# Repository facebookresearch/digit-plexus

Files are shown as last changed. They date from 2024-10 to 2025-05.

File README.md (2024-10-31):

# Meta Digit Plexus
##### A robotics hardware platform for the integration sensors and end effectors into a common platform.

<p align="center">
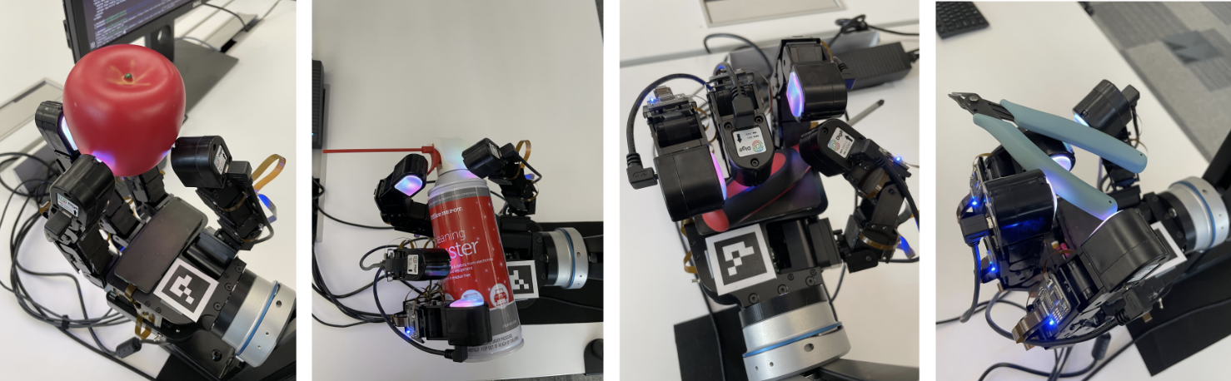
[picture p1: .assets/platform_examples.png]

</p>

<p align="center">
    
</p>

Digit Plexus aims to create a standardized platform that provides a hardware-software solution to integrate tactile sensors on any robot hand. The platform interfaces vision-based and skin-based tactile sensors like Digit, Digit 360, and [ReSkin](https://reskin.dev) across fingertips, fingers, and palm, into control boards to encode all data to a host computer. The software integration and hardware components of the platform allows for seamless data collection, control and analysis over a single cable.

## Standardized Platform

We propose and implement variations of the Digit Plexus standardized architecture found [here](./docs/digit-plexus.pdf)

The [advanced](./hardware/schematics/advanced/) variation of the architecture allows for a modular implementation to support any custom sense patch configuration where each link is connected via USB to the hand logic motherboard. 

Additionally, actions may be provided to a robotic end effector or hand via multiple methods such as: CAN, USB, I2C. 

#### Partnerships

We have partnered with Wonik Robotic's to develop a next generation Allegro Hand based off of the Digit Plexus platform. For early access, interest may be expressed through this [form](https://digit.ml/plexus).

## Usage

Design files for **basic** (rigid based) and **advanced** (flex) are found in the [hardware](./hardware/) folder of the repository. Furthermore, we provide the Altium Designer ECAD templates which can be used to create a custom sensor patch configuration for the hand, links or fingertips. 

### Sense and Hand Patch

Mechanical sense patch files for 3D printing or mold design are found in the [mechanical](./mechanical/) folder. Depending on the application, or the preferred sensing modality, you may use a similar technique to ReSkin (magnetic particulate infused silicone) or an alternative composition of silicone for forming the sensing surface interacting with the sense patch. We recommend attaching the sense patches to the base end effector with a 3M 300LSE double sided adhesive. 

### Fingertip Sensing

The Digit Plexus platform supports Digit tactile sensors as well as any alternative sensor based on a USB2.0 connection as shown [here](./docs/digit-plexus-digit-v1.pdf).

<p align="center">
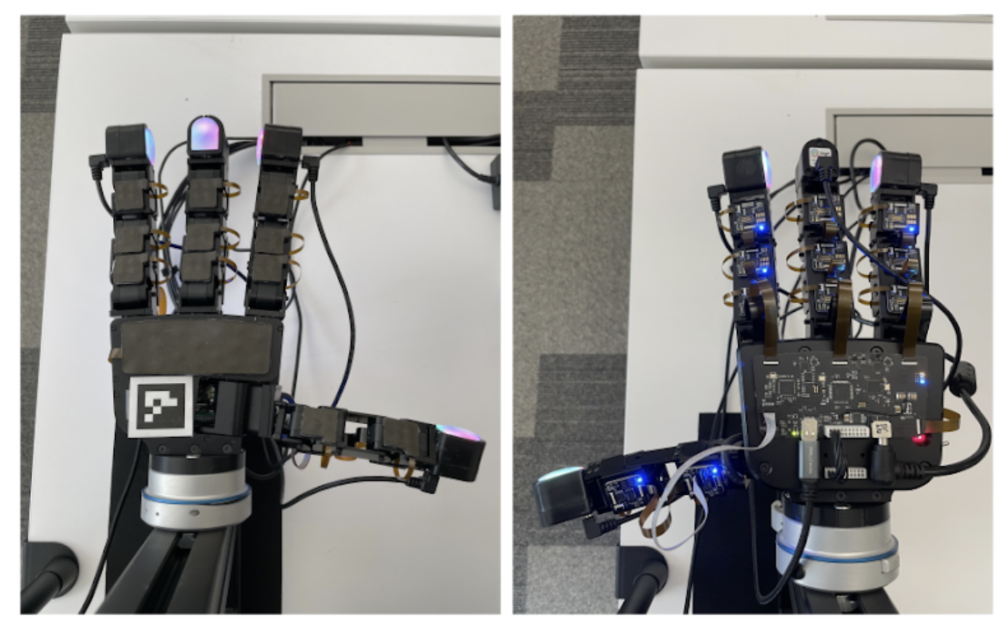
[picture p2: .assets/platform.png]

</p>

## 🛠️Installation and setup
Digit Plexus contains a USB hub device which will enumerate all devices connected to the [base](./hardware/base).

Currently, this supports the [Allegro Hand](https://www.allegrohand.com/) and the [next generation Allegro Hand](https://digit.ml/plexus.html) in partnership with Meta.

Digit Plexus provides a new interface for controlling the Allegro Hand directly through a Python interface, as well provides a ROS2 integration.

Installation and usage instructions are found [here](./plexus/README.md).

## Related Works using Digit Plexus plartform
* [Neural feels with neural fields: Visuo-tactile perception for in-hand manipulation, Sudharshan Suresh et al.](https://suddhu.github.io/neural-feels/)
* [Learning In-Hand Translation Using Tactile Skin With Shear and Normal Force Sensing, Jessica Yin et al.](https://jessicayin.github.io/tactile-skin-rl/)

## License
This project is licensed under [LICENSE](LICENSE).

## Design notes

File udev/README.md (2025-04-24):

# Device Install
Scripts necessary to install physical devices, configure permissions and attributes. 

### Install `udev` Device Rules

```
sudo ./install_devices.sh
```

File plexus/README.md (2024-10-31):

# Digit Plexus 
This guide will help you set up the environment, build the ROS2 package Digit Plexus , and join the growing community of developers and researchers.

## 🛠 Virtual Environment Setup

To install and activate the virtual environment for Digit Plexus, run the following commands:

```
cd digit-plexus
./plexus/install_plexus_venv.sh
```
This will handle the necessary dependencies and ensure your environment is ready for development.

## 🛠 Build ROS2 pkg
```
mkdir -p plexus_ws/src
cd plexus_ws/src
git clone https://github.com/facebookresearch/digit-plexus.git
cd ..
sh ./src/digit-plexus/plexus/ros2/plexus_pkg/colcon_build.sh
```

## 🛠 Install Digit Plexus  pkg
```
cd plexus_ws/src/digit-plexus/
pip install -e .
```

This creates the workspace, builds the source, and prepares everything for use with ROS2 nodes and topics.

## 🚀 Run Commands 
To launch the Digit Plexus package, use the following command:

This launches the allegro hand with plexus.
```bash
ros2 launch plexus_pkg allegro_hand_launch.py
```

For Sensor Patch
```
ros2 launch plexus_pkg sensor_patch_launch.py
```

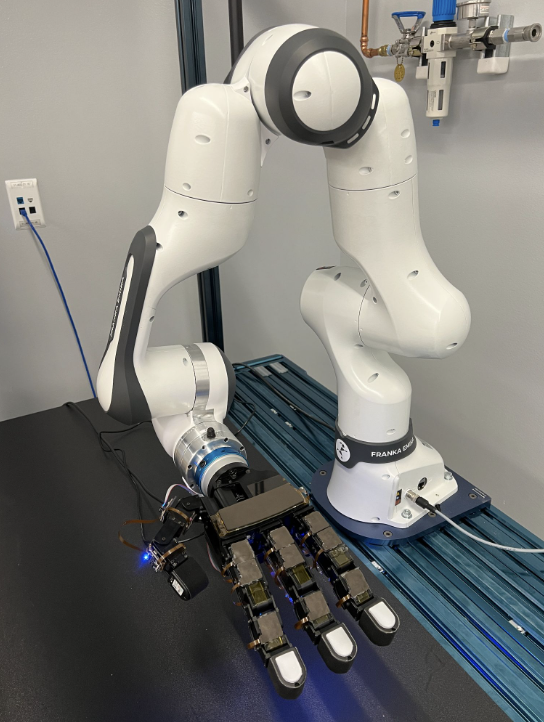
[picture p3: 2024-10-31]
.assets/arm_platform.png

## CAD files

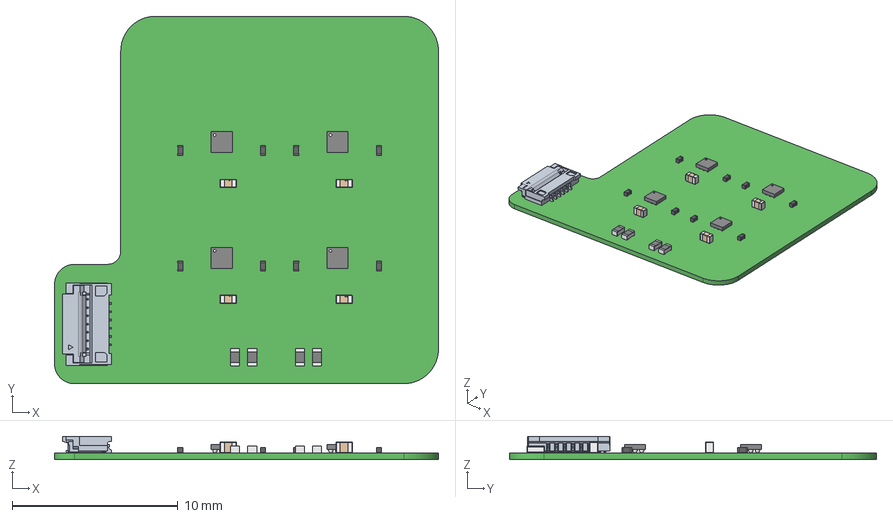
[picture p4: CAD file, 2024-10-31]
mechanical/plexus_finger_link_sense_patch.step
23.2 x 22.2 x 1.41 mm
ball x 36
Mid_Body x 4
Mark x 4
TDK Logo x 4
Cap_Murata_GRM155R71C104KA88D_eec x 8

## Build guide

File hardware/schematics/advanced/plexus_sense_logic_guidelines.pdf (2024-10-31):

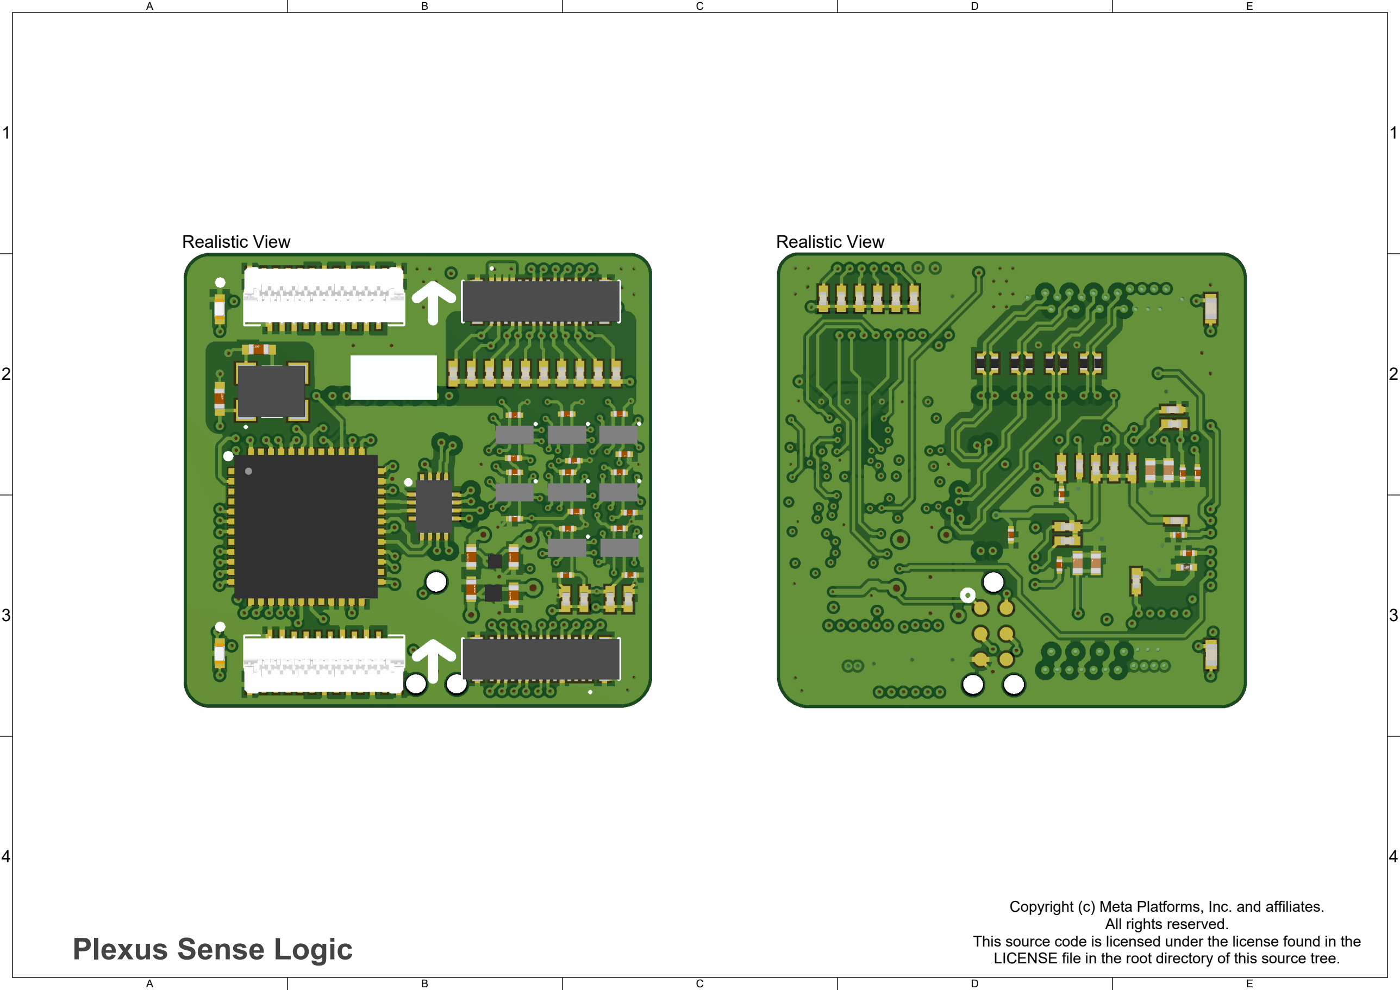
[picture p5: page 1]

A

B

C

D

E

1 | 1
2 | 2
3 | 3
4 | 4
Realistic View | Realistic View

# Plexus Sense Logic

Copyright (c) Meta Platforms, Inc. and affiliates.
All rights reserved.
This source code is licensed under the license found in the LICENSE file in the root directory of this source tree.

1 | 1
2 | 2
3 | 3
4 | 4

STACKUP SUMMARY:
A. NUMBER OF COPPER LAYERS: 8
B. BOARD THICKNESS SHALL BE 1.6mm +/- 10%
C. COPPER: See Layer Stack
D. DEFAULT TRACE/SPACE: 5mil / 5mil
E. CONDUCTOR WIDTH TOLERANCE = +/- 0.01mm

1.

2. SURFACE FINISH/PLATING: ENIG
SOLDERMASK WITH LIQUID PHOTO IMAGEABLE (LPI) PER IPC-SM-840C, CLASS T. COLOR: MATTE BLACK

3.

LOCATE MANUFACTURER'S IDENTIFICATION AND LOT CODE ON PRIMARY SIDE FREE FROM ALL METAL ENTITY RENDERED IN SILKSCREEN.

4.

DETAILS NOT SPECIFIED ARE AT MANUFACTURER'S OPTION BUT FINAL APPROVAL MUST BE OBTAINED

5.

NOTES: UNITS IN MILLIMETERS UNLESS OTHERWISE SPECIFIED

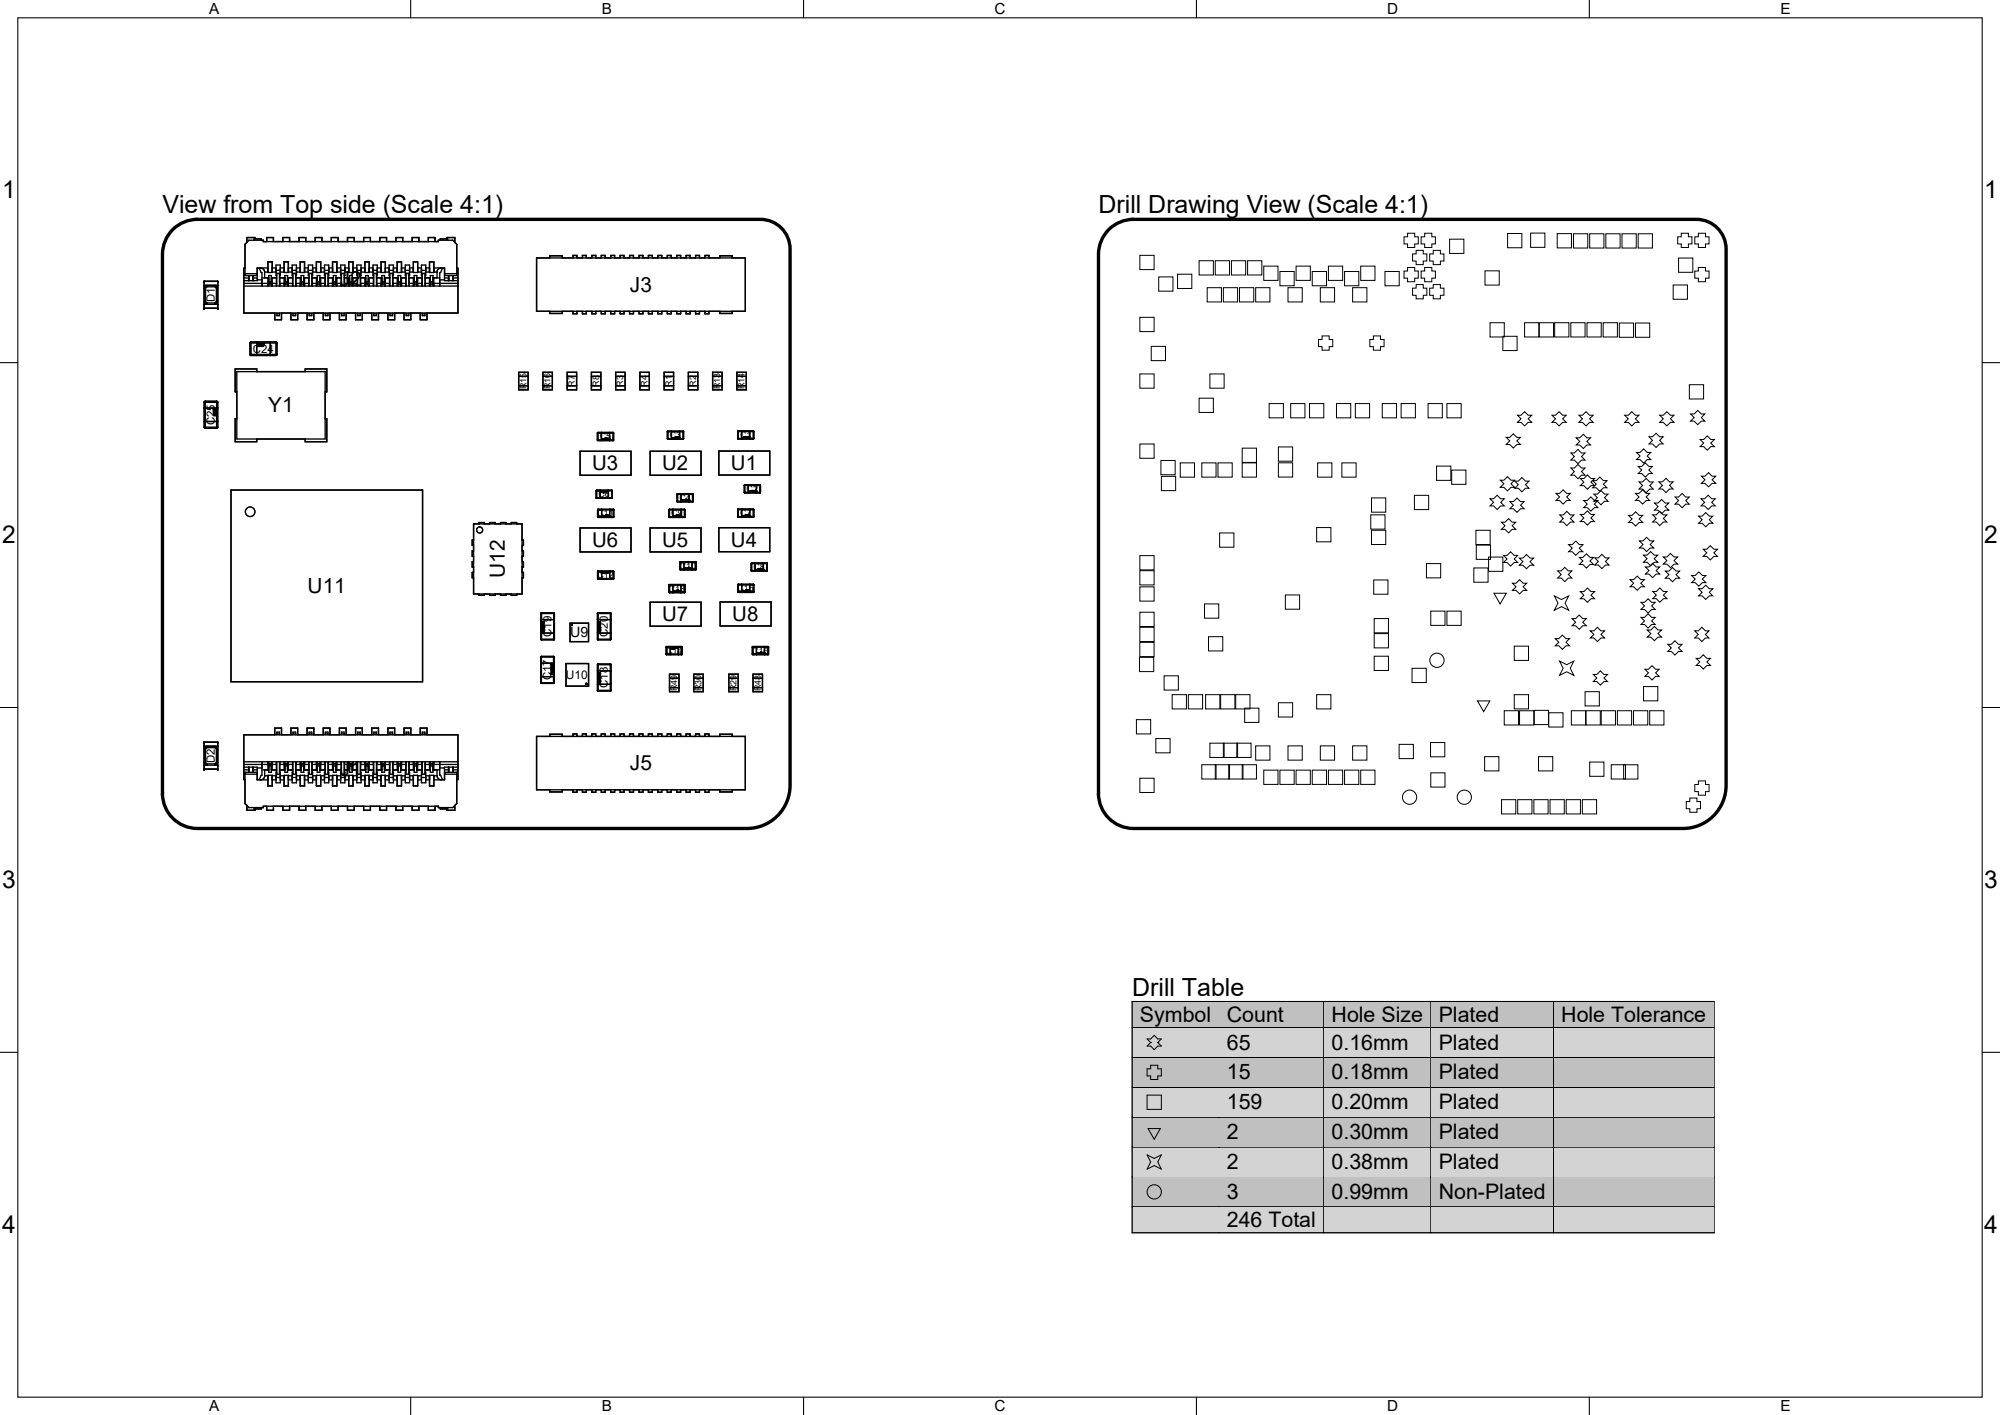
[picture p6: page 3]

View from Top side (Scale 4:1)

Drill Drawing View (Scale 4:1)

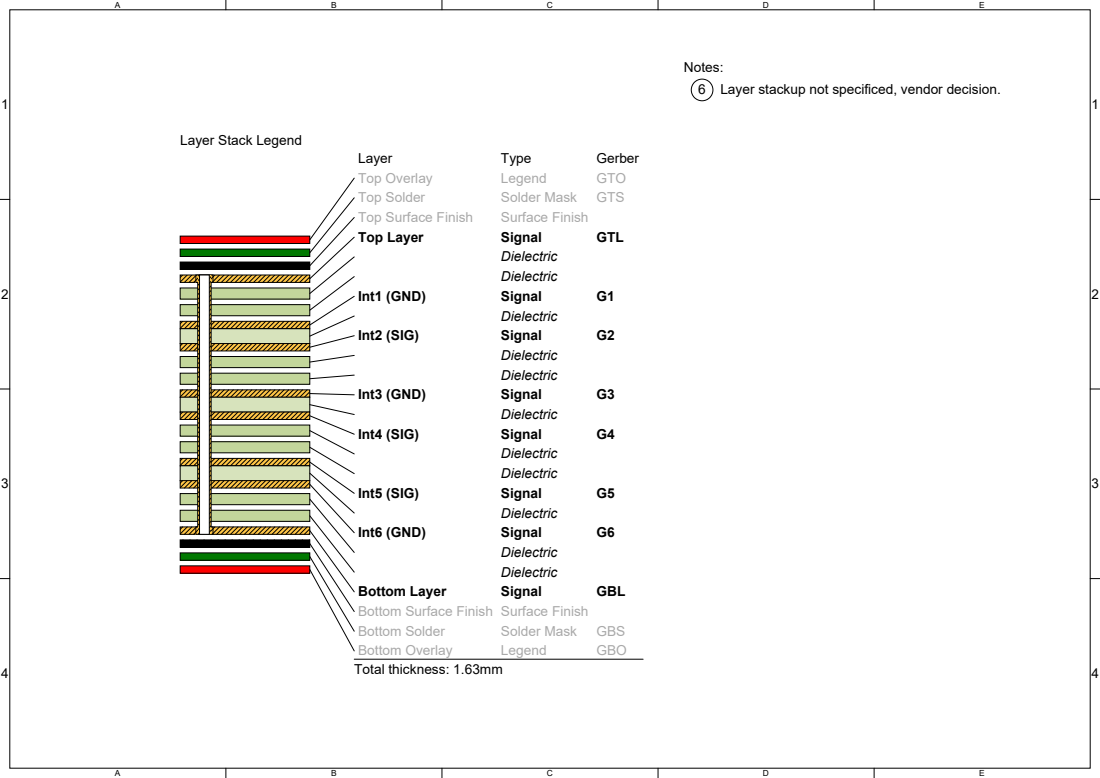
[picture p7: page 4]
Layer; Type; Gerber; Top Overlay; Legend; GTO; Top Solder; Solder Mask; GTS; Top Surface Finish; Surface Finish; Top Layer; Signal; GTL; Dielectric Dielectric; Int1 (GND); Dielectric; Int2 (SIG); Int3 (GND); Int4 (SIG); Int5 (SIG); Int6 (GND); Bottom Layer; GBL; Bottom Solder; GBS; Bottom Overlay; GBO

Notes:
6 Layer stackup not specificed, vendor decision.

Layer Stack Legend

Bottom Surface Finish Surface Finish
Total thickness: 1.63mm

1 | 1
2 | 2
3 | 3
4 | 4

Impedance Id
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
Target Impedance
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
Calculated Impedance
90.02
86.29
86.29
86.29
86.29
86.29
86.29
90.02

Trace layer
Top Layer
Int1 (GND)
Int2 (SIG)
Int3 (GND)
Int4 (SIG)
Int5 (SIG)
Int6 (GND)
Bottom Layer

Wide Trace Width
6.54mil
5.50mil
5.50mil
5.50mil
5.50mil
5.50mil
5.50mil
6.54mil

Narrow Trace Width
6.54mil
5.50mil
5.50mil
5.50mil
5.50mil
5.50mil
5.50mil
6.54mil

Reference layers
Int1 (GND)
Top Layer,Int2 (SIG)
Int1 (GND),Int3 (GND)
Int2 (SIG),Int4 (SIG)
Int3 (GND),Int5 (SIG)
Int4 (SIG),Int6 (GND)
Int5 (SIG),Bottom Layer
Int6 (GND)

Clearance
5.00mil
5.00mil
5.00mil
5.00mil
5.00mil
5.00mil
5.00mil
5.00mil

Target Tolerance
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
Transmission Line Structure Table

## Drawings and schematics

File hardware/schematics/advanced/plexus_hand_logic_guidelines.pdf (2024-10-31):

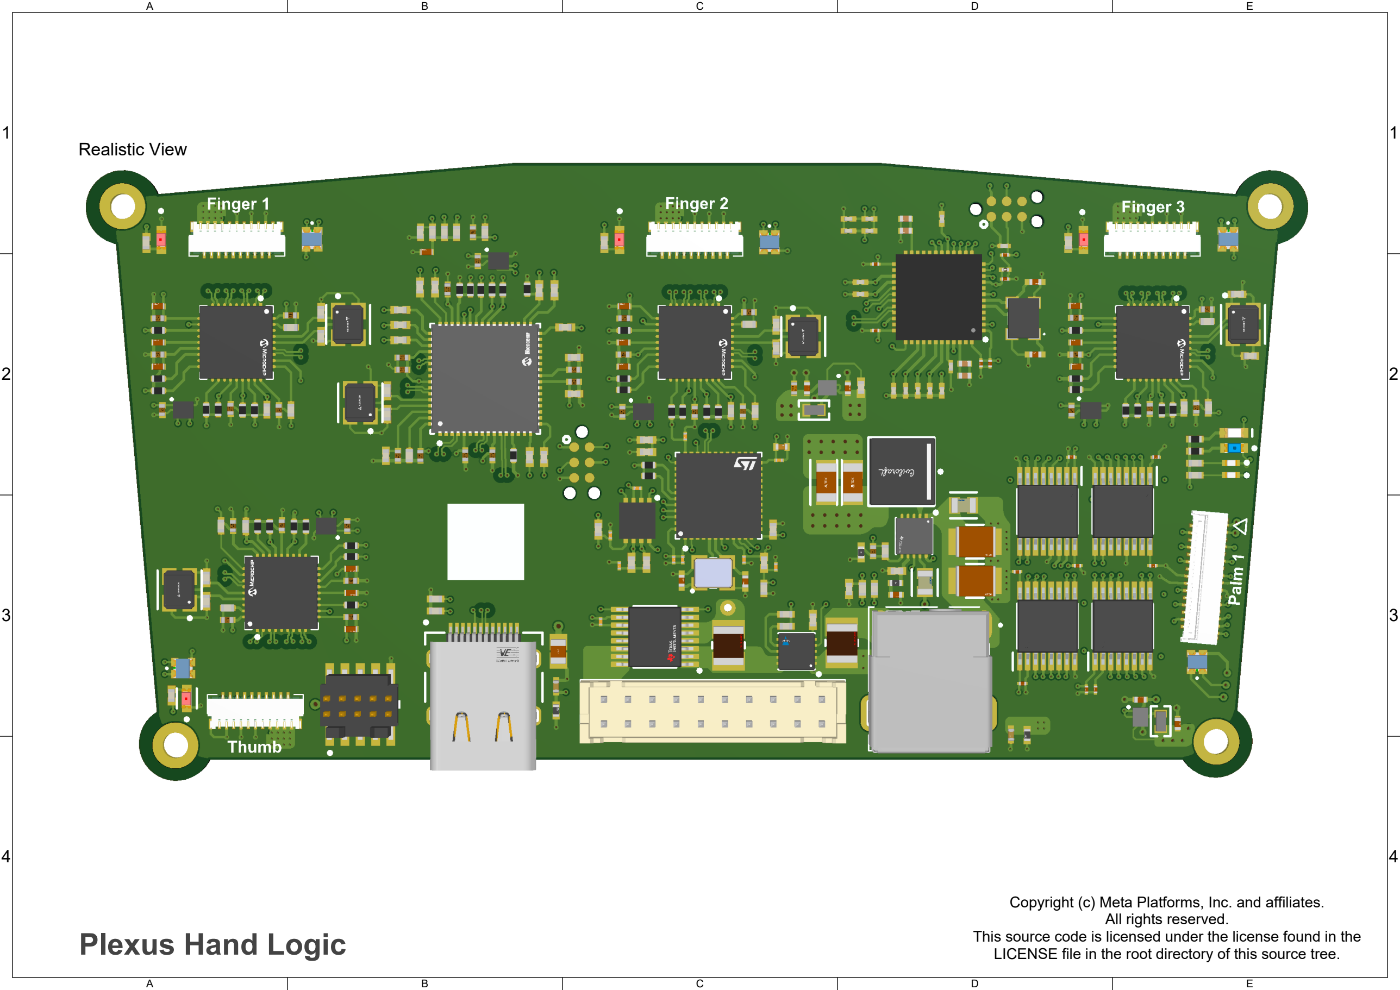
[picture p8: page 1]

A

B

C

D

E

1 | 1
2 | 2
3 | 3
4 | 4

Realistic View

# Plexus Hand Logic

Copyright (c) Meta Platforms, Inc. and affiliates.
All rights reserved.
This source code is licensed under the license found in the LICENSE file in the root directory of this source tree.

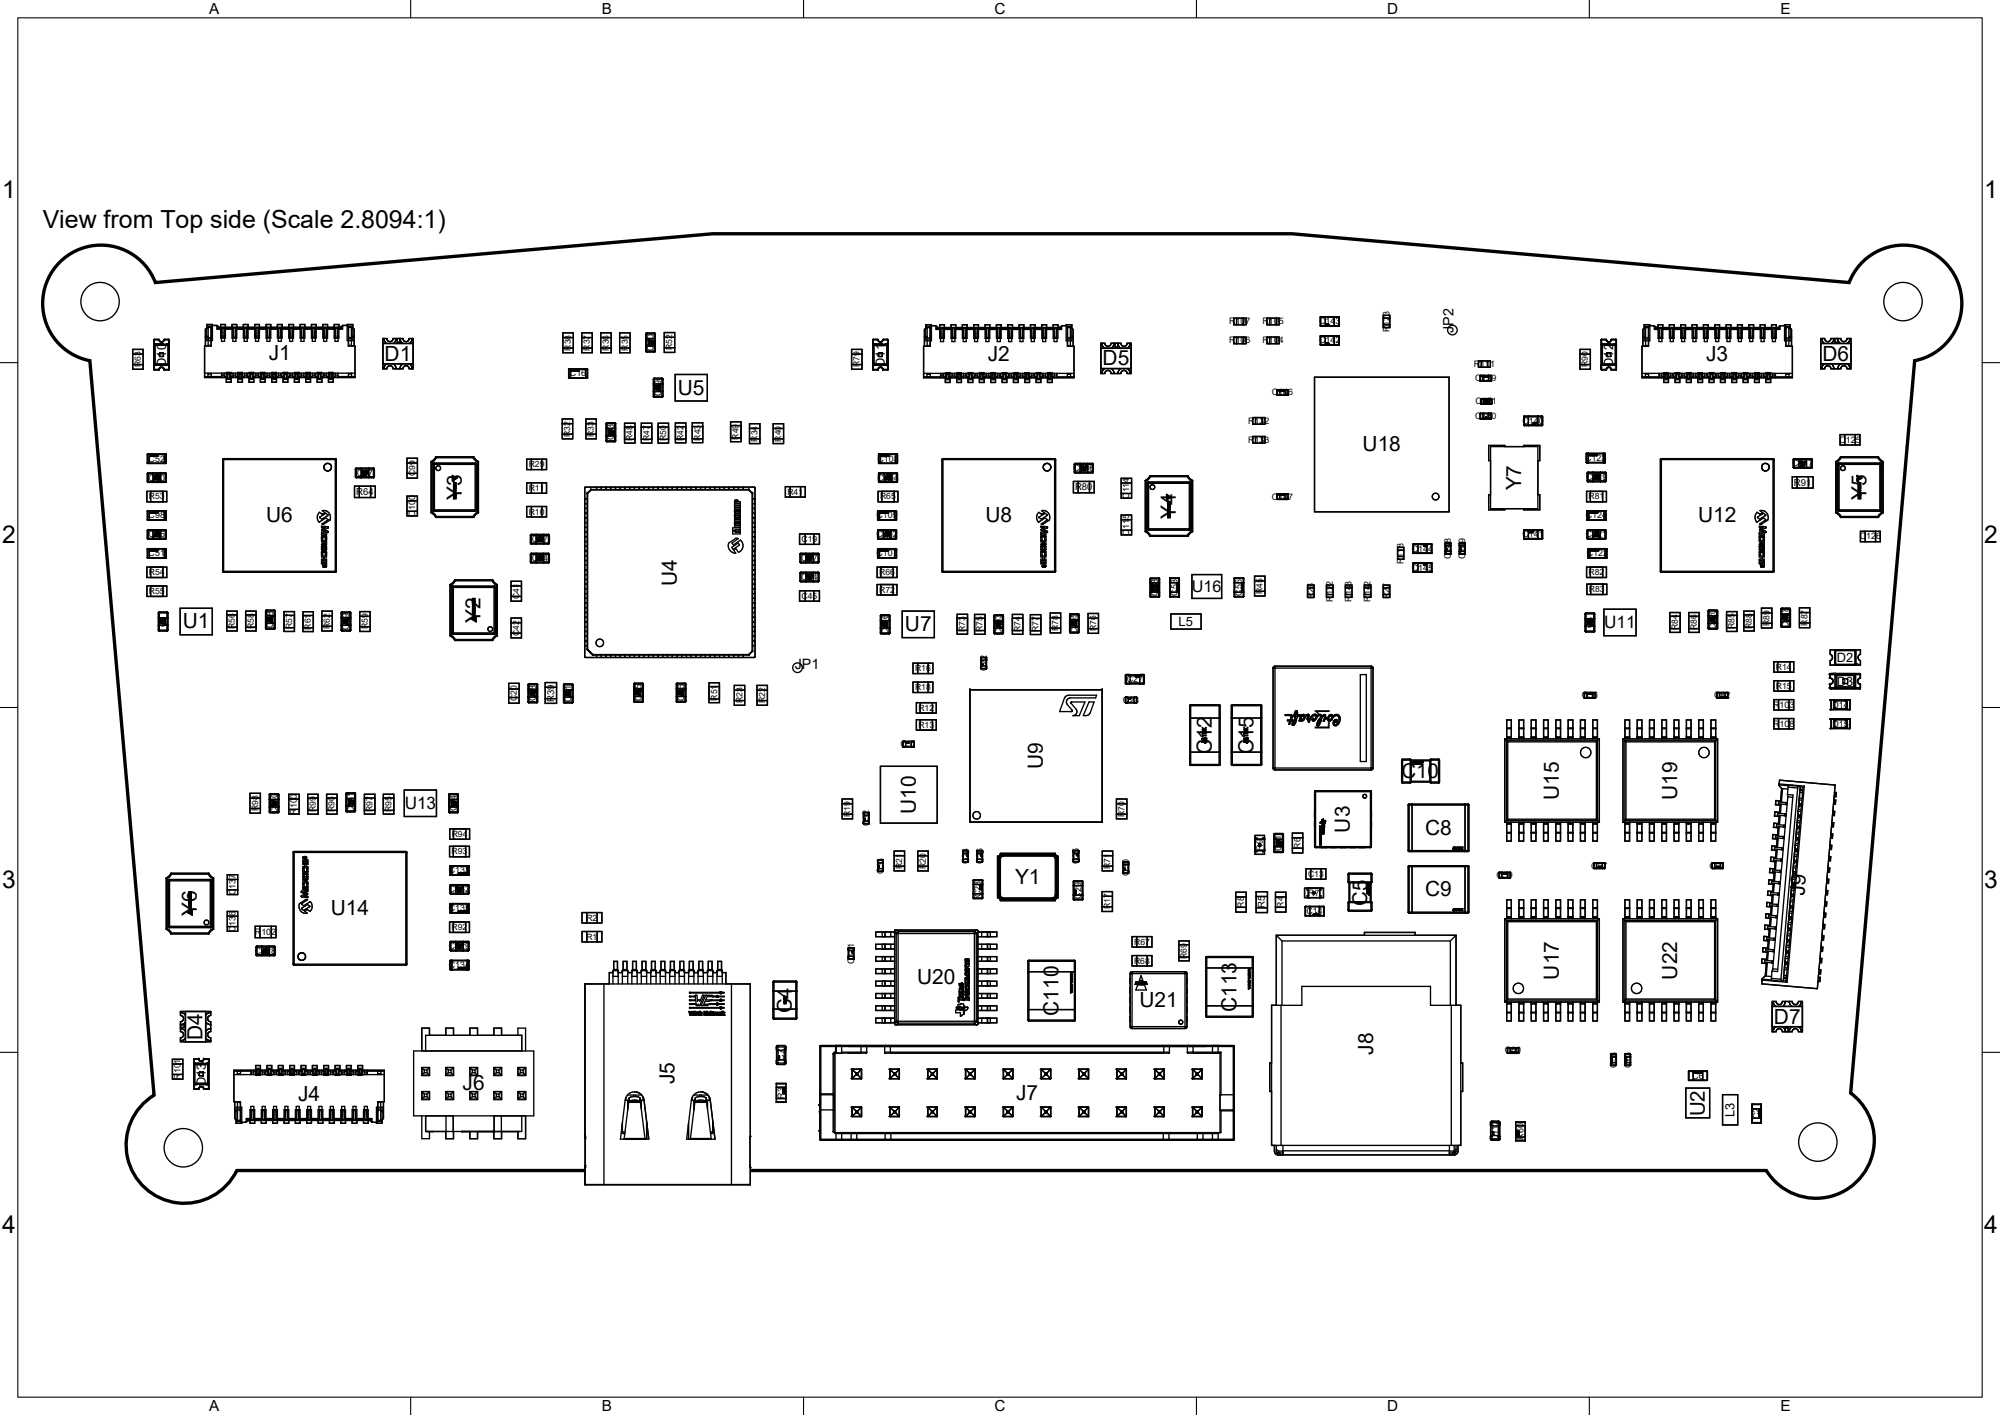
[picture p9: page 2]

View from Top side (Scale 2.8094:1)

1 | 1
2 | 2
3 | 3
4 | 4

STACKUP SUMMARY:
A. NUMBER OF COPPER LAYERS: 8
B. BOARD THICKNESS SHALL BE 62mil +/- 10%
C. COPPER: See Layer Stack
D. DEFAULT TRACE/SPACE: 5mil / 5mil
E. CONDUCTOR WIDTH TOLERANCE = +/- 0.01mm

1.

SURFACE FINISH/PLATING:
A. BOARD SHALL BE IMMERSION GOLD PLATED (ENIG)

2.

SOLDERMASK WITH LIQUID PHOTO IMAGEABLE (LPI) PER IPC-SM-840C, CLASS T. COLOR: MATTE BLACK

3.

LOCATE MANUFACTURER'S IDENTIFICATION AND LOT CODE ON PRIMARY SIDE FREE FROM ALL METAL ENTITY RENDERED IN SILKSCREEN.

4.

DIFFERENTIAL CONTROLLED IMPEDANCE REQUIRED ON BOARD.
SEE TABLE : DIFFERENTIAL CONTROLLED IMPEDANCE
SEE TABLE : SINGLE ENDED CONTROLLED IMPEDANCE

5.

DETAILS NOT SPECIFIED ARE AT MANUFACTURER'S OPTION BUT FINAL APPROVAL MUST BE OBTAINED

6.

NOTES: UNITS IN MILLIMETERS UNLESS OTHERWISE SPECIFIED

# Note: Vendor preferred

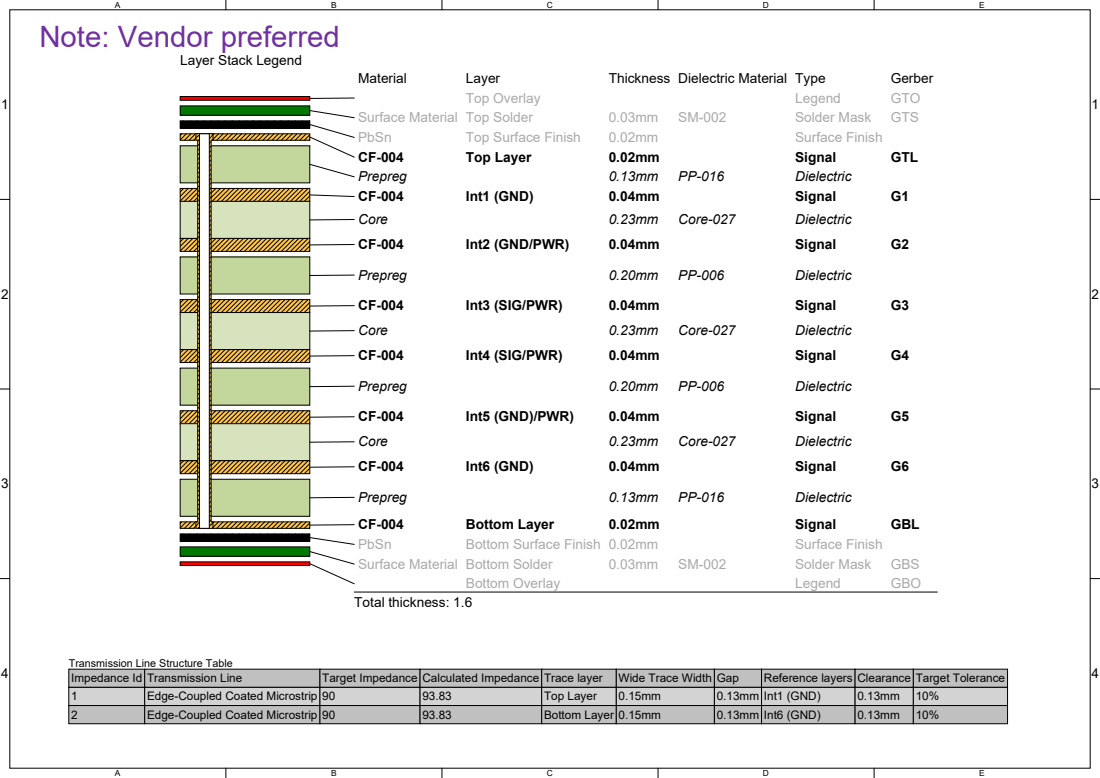
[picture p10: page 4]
Material; Layer; Thickness Dielectric Material Type; Gerber; Top Overlay; Legend; GTO; Surface Material Top Solder; Solder Mask; GTS; PbSn; Top Surface Finish; Surface Finish; Top Layer; Signal; GTL; Prepreg; Dielectric; Int1 (GND); Core; Core-027; Int2 (GND/PWR); Int3 (SIG/PWR); Int4 (SIG/PWR); Int5 (GND)/PWR); Int6 (GND); Bottom Layer; GBL; Bottom Surface Finish 0.02mm; Surface Material Bottom Solder; GBS; Bottom Overlay; GBO; Total thickness: 1.6; Target Impedance 90 90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

Layer Stack Legend

Transmission Line Structure Table
Impedance Id

Transmission Line
Edge-Coupled Coated Microstrip

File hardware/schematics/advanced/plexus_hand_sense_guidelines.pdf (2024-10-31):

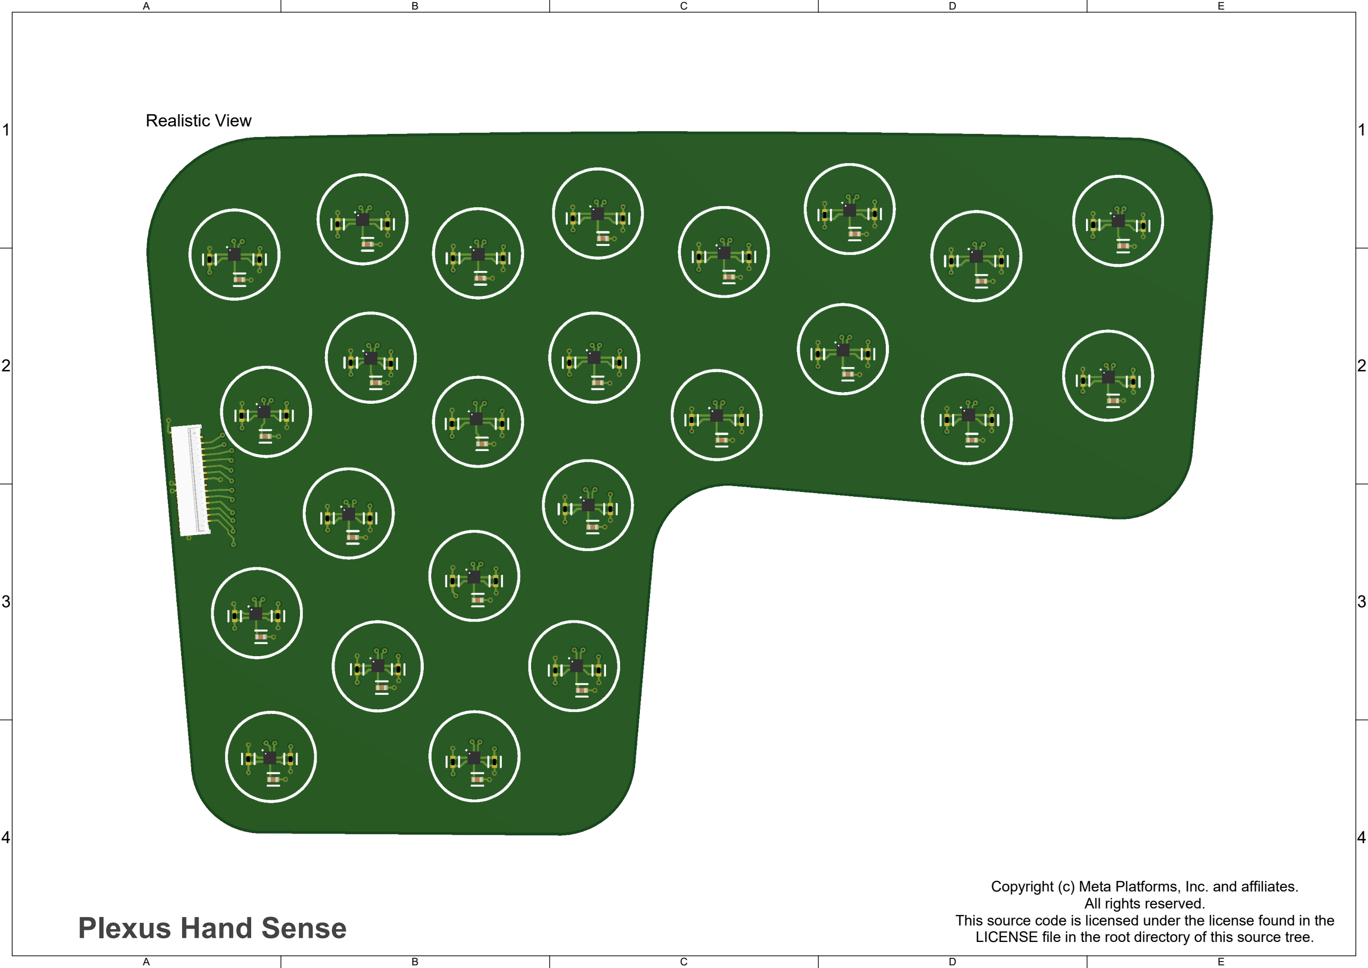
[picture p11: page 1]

A

B

C

D

E

1 | 1
2 | 2
3 | 3
4 | 4

Realistic View

# Plexus Hand Sense

Copyright (c) Meta Platforms, Inc. and affiliates.
All rights reserved.
This source code is licensed under the license found in the LICENSE file in the root directory of this source tree.

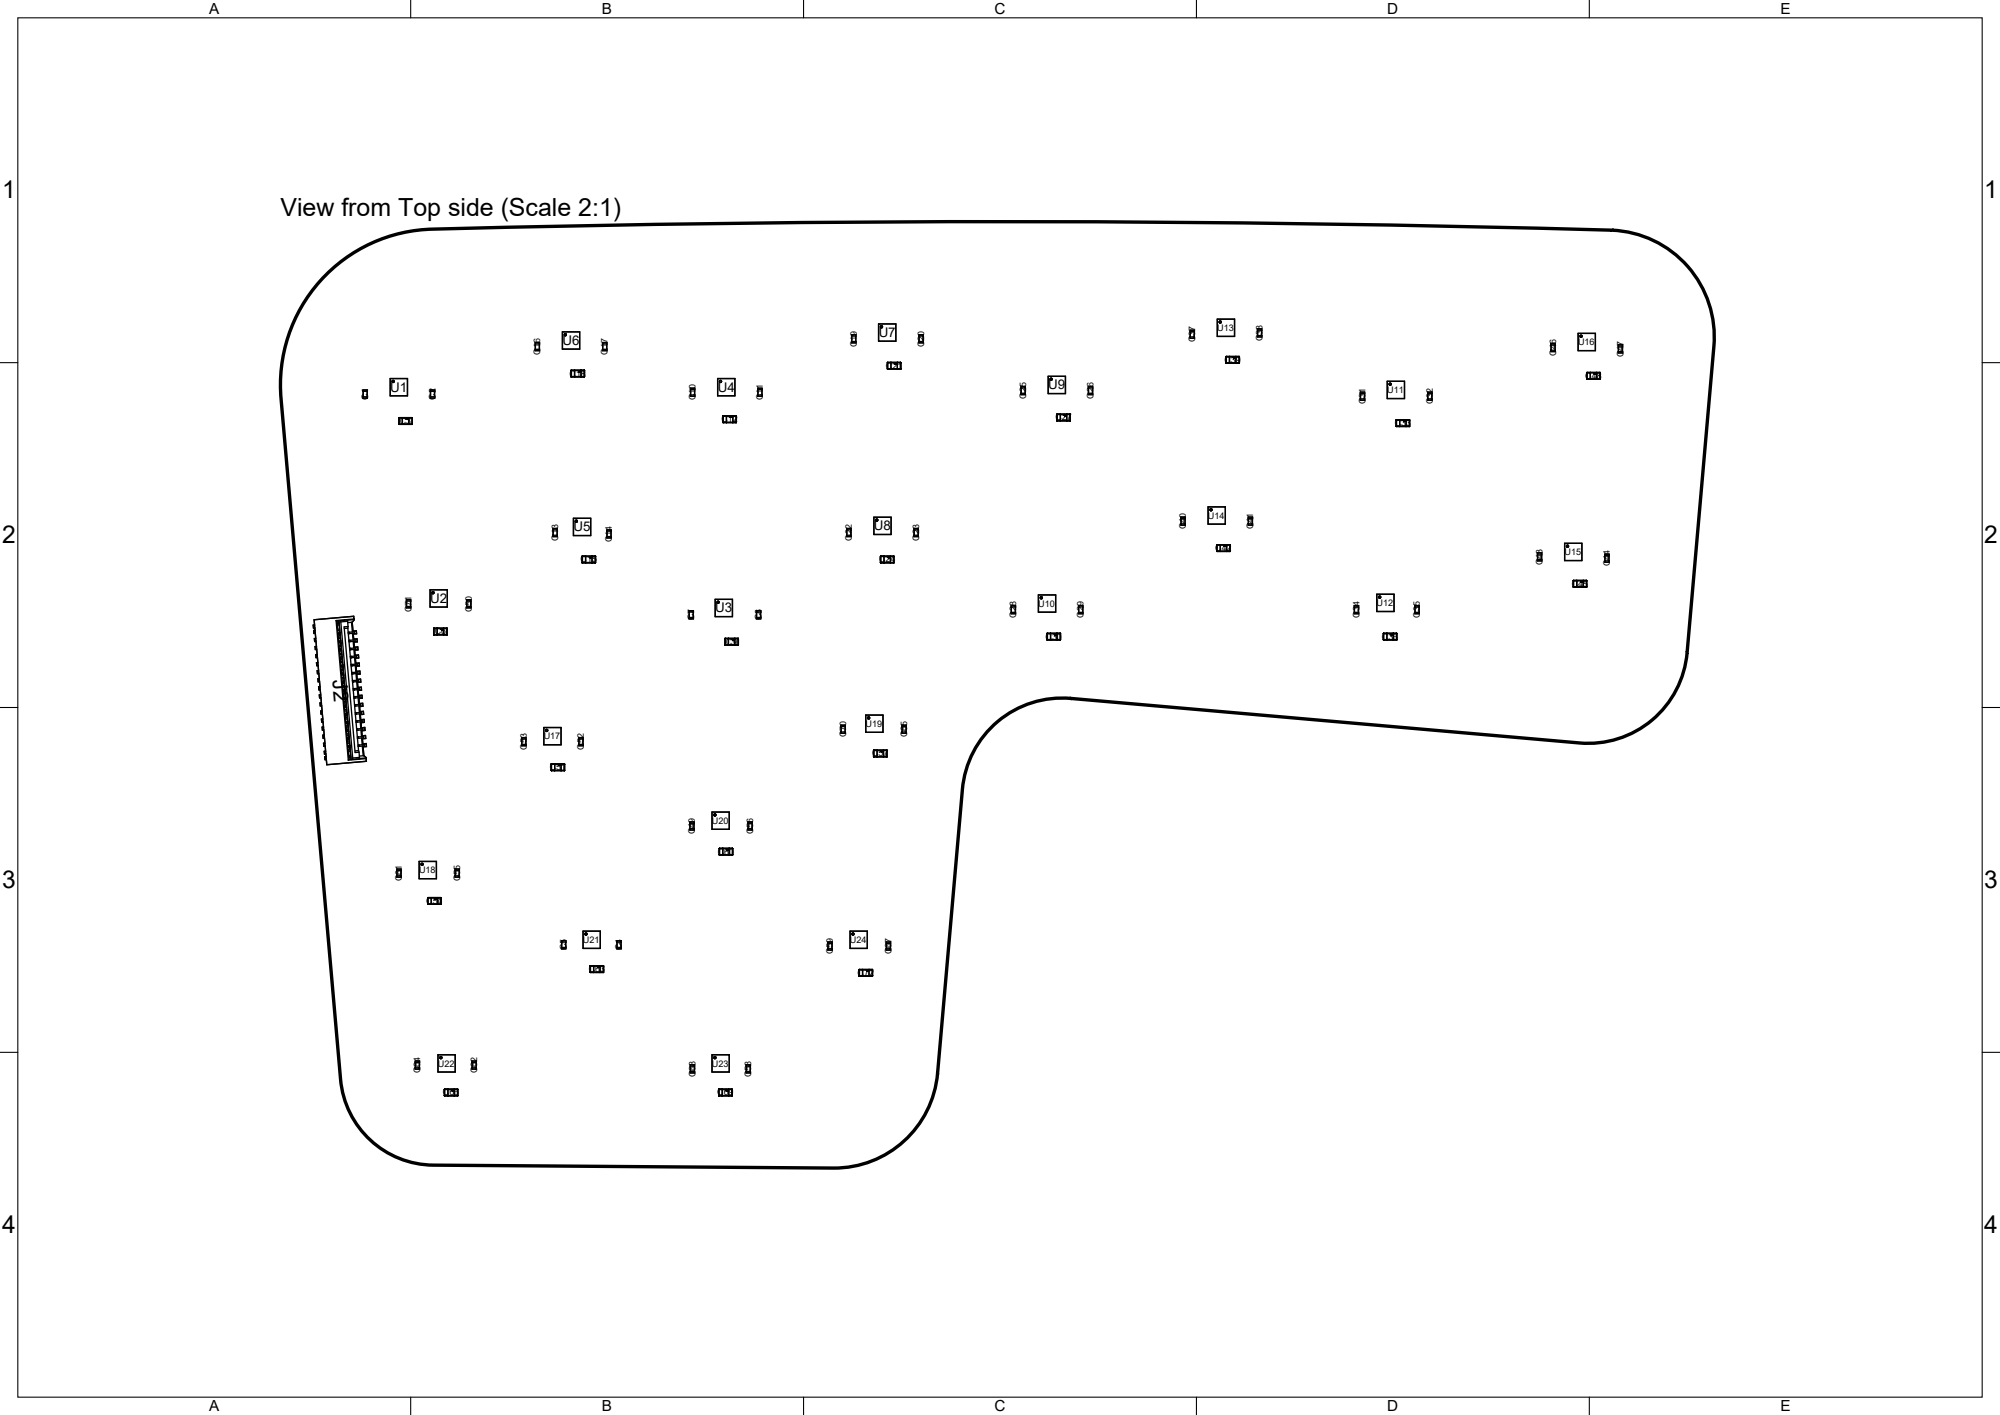
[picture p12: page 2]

View from Top side (Scale 2:1)

1 | 1
2 | 2
3 | 3
4 | 4

STACKUP SUMMARY:
A. NUMBER OF COPPER LAYERS: 4
B. BOARD THICKNESS SHALL BE 1.2mm
C. COPPER: See Layer Stack
D. DEFAULT TRACE/SPACE: 5mil / 5mil
E. CONDUCTOR WIDTH TOLERANCE = +/- 0.01mm

1.

SURFACE FINISH/PLATING:
A. BOARD SHALL BE IMMERSION GOLD PLATED (ENIG)

2.

SOLDERMASK WITH LIQUID PHOTO IMAGEABLE (LPI) PER IPC-SM-840C, CLASS T. COLOR: MATTE BLACK

3.

LOCATE MANUFACTURER'S IDENTIFICATION AND LOT CODE ON PRIMARY SIDE FREE FROM ALL METAL ENTITY RENDERED IN SILKSCREEN.

4.

DETAILS NOT SPECIFIED ARE AT MANUFACTURER'S OPTION BUT FINAL APPROVAL MUST BE OBTAINED

5.

NOTES: UNITS IN MILLIMETERS UNLESS OTHERWISE SPECIFIED

Note: 1.2mm thickness, standard or default stackup is accepted.

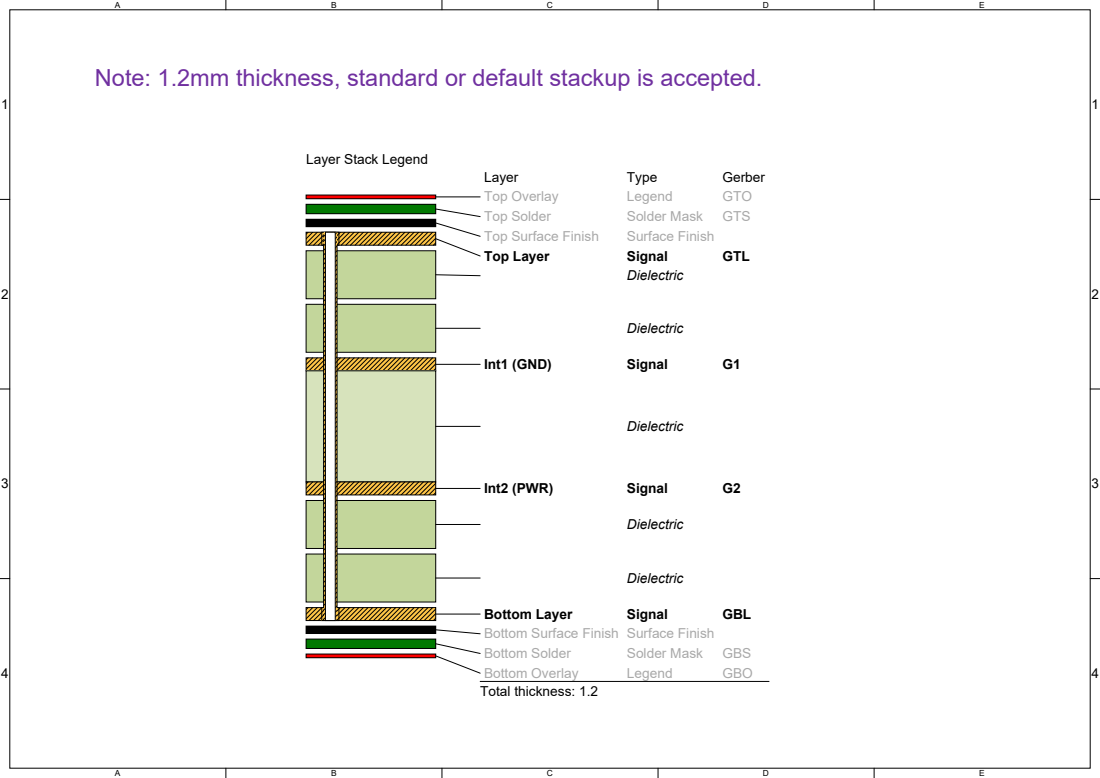
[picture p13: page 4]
Layer; Type; Gerber; Top Overlay; Legend; GTO; Top Solder; Solder Mask; GTS; Top Surface Finish; Surface Finish; Top Layer; Signal; GTL; Dielectric; Int1 (GND); Int2 (PWR); Bottom Layer; GBL; Bottom Solder; GBS; Bottom Overlay; GBO

Layer Stack Legend

Bottom Surface Finish Surface Finish
Total thickness: 1.2

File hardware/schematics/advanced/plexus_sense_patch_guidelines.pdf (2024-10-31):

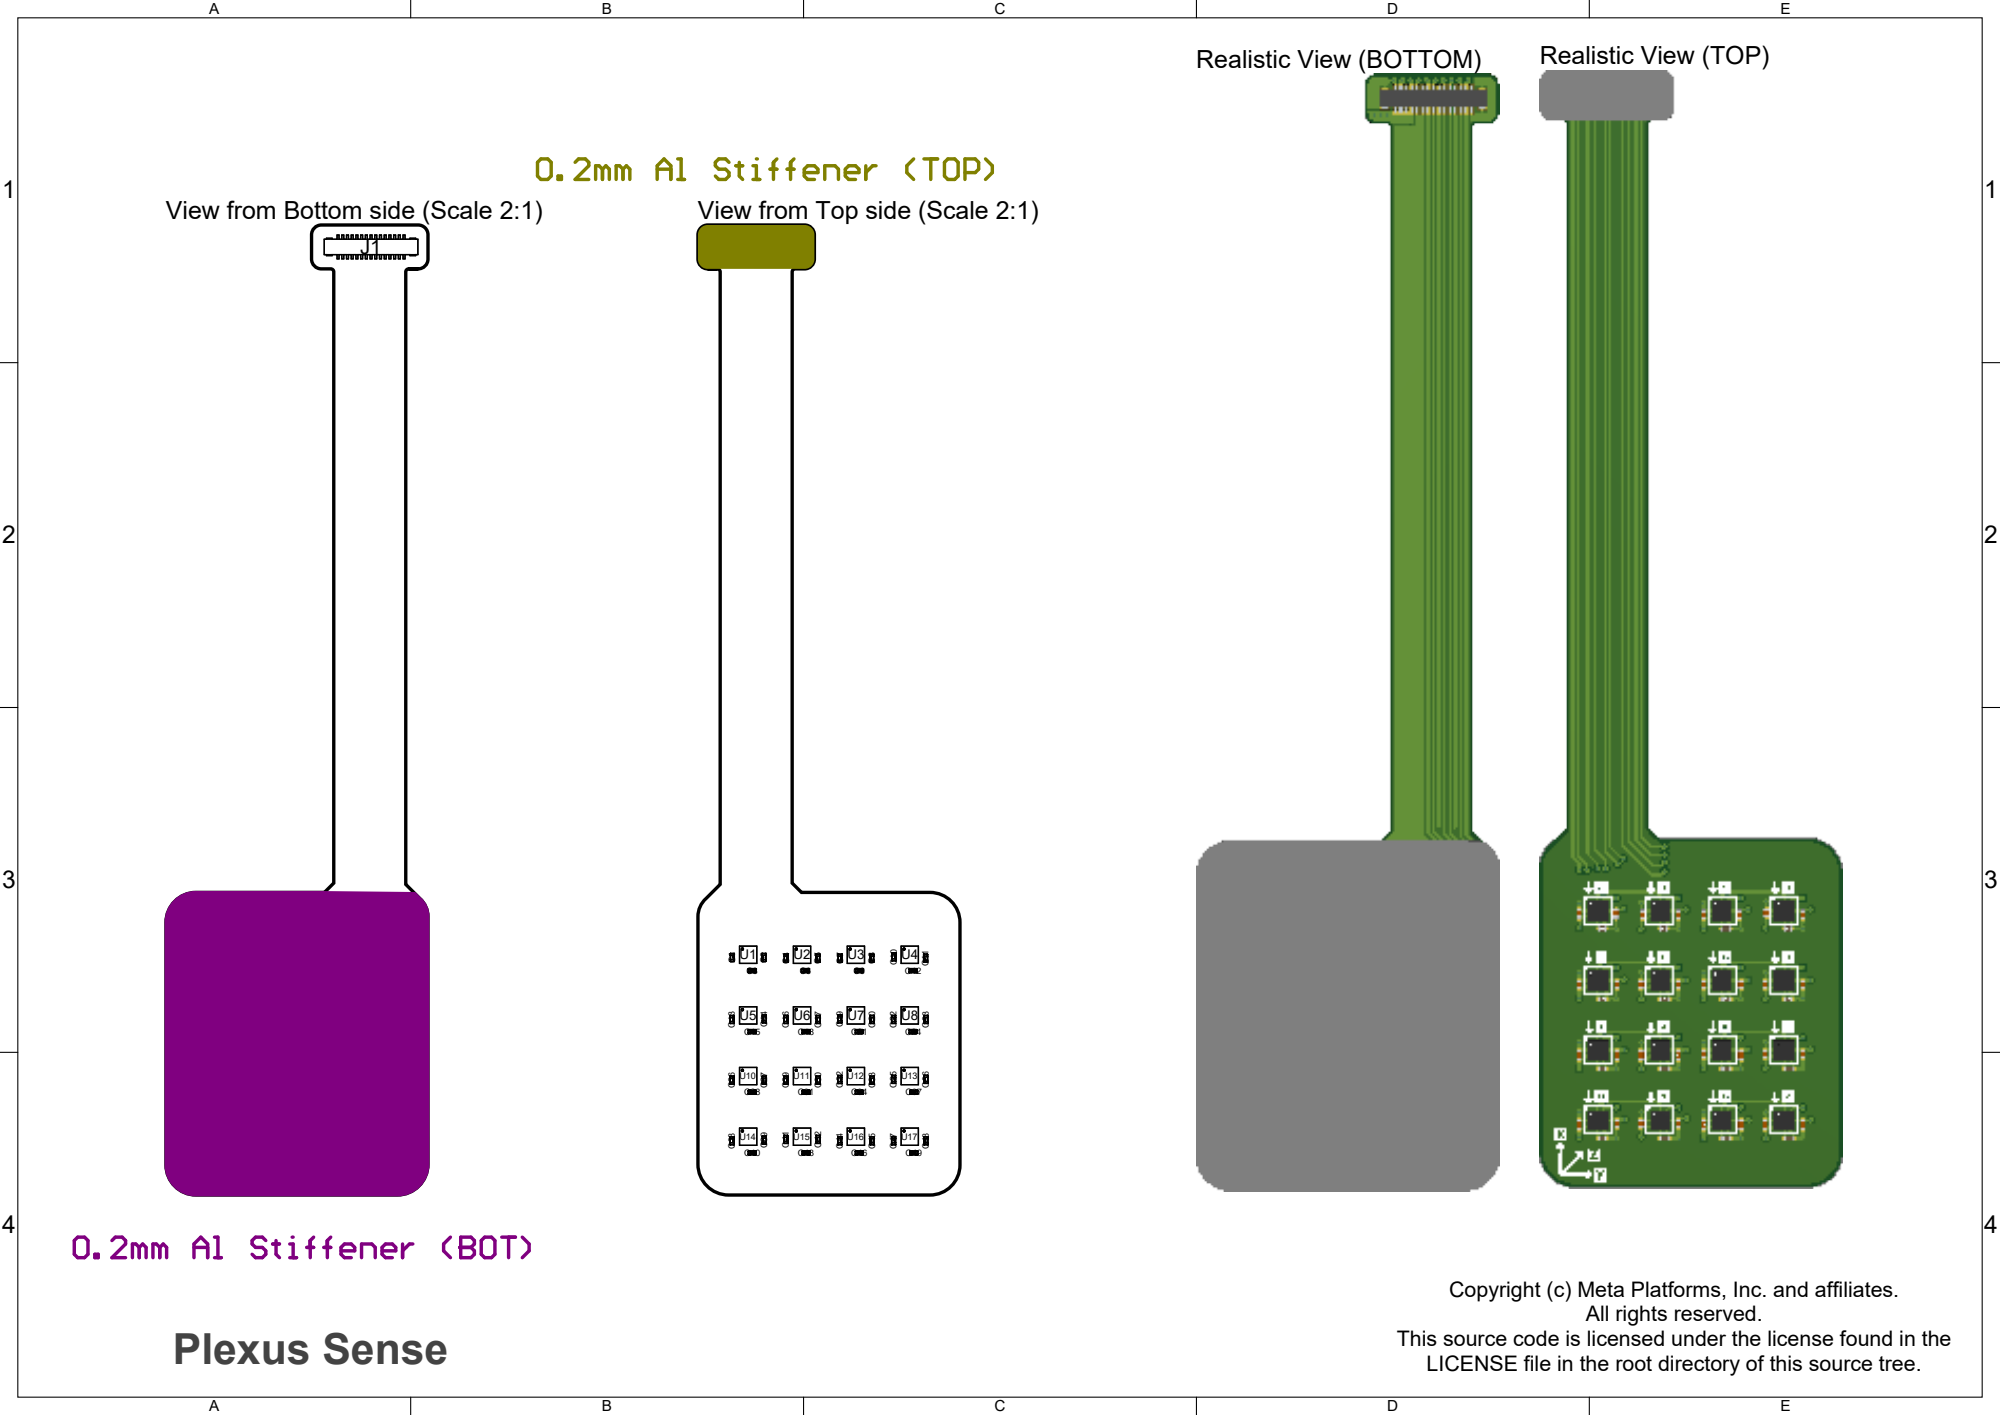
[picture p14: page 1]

View from Bottom side (Scale 2:1)

View from Top side (Scale 2:1)

Copyright (c) Meta Platforms, Inc. and affiliates.

This source code is licensed under the license found in the

1 | 1
2 | 2
3 | 3
4 | 4
1. INTERPRET THIS DRAWING IN ACCORDANCE WITH IPC-D-325A
2. BOARD FABRICATION AND QUALITY PER IPC-6012, CLASS 2, EXCEPT SPECIFIED HEREIN
3. DIMENSIONAL LIMITS APPLY AFTER PLATING OR COATING
STACKUP SUMMARY:
A. NUMBER OF COPPER LAYERS: 4
B. BOARD THICKNESS SHALL BE: 0.20mm - 0.33mm +/- 10% (optimize for fab speed)
C. COPPER: See Layer Stack
D. DEFAULT TRACE/SPACE: 5mil / 5mil
E. CONDUCTOR WIDTH TOLERANCE = +/- 0.01mm

4.

SURFACE FINISH/PLATING:
A. BOARD SHALL BE IMMERSION GOLD PLATED (ENIG) ACCORDING TO IPC-4552. THICKNESS SHALL BE A MINIMUM OF 0.05μm GOLD OVER 3-6μm NICKEL

5.

SOLDERMASK WITH LIQUID PHOTO IMAGEABLE (LPI) PER IPC-SM-840C, CLASS T. COLOR: BLACK COVERLAY

6.

SILKSCREEN PER SUPPLIED ARTWORK WITH ORGANIC, NON-CONDUCTIVE, EPOXY INK. SILKSCREEN MAY BE TRIMMED OFF ANY SOLDERABLE ENTITY.
COLOR: WHITE

7.

LOCATE MANUFACTURER'S IDENTIFICATION AND LOT CODE ON BOTTOM SIDE FREE FROM ALL METAL ENTITY RENDERED IN SILKSCREEN.

8.

DETAILS NOT SPECIFIED ARE AT MANUFACTURER'S OPTION BUT FINAL APPROVAL MUST BE OBTAINED

9.

NOTES: UNITS IN MILLIMETERS UNLESS OTHERWISE SPECIFIED

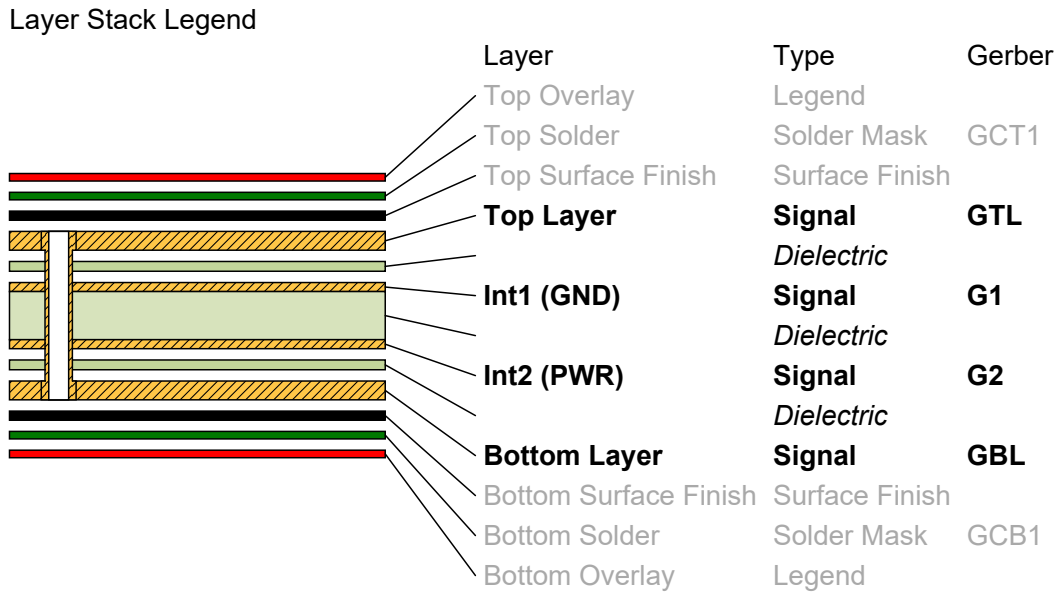
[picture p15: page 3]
Layer; Type; Gerber; Top Overlay; Legend; Top Solder; Solder Mask; GCT1; Top Surface Finish; Surface Finish; Top Layer; Signal; GTL; Dielectric; Int1 (GND); Int2 (PWR); Bottom Layer; GBL; Bottom Solder; GCB1; Bottom Overlay

Layer Stack Legend

Bottom Surface Finish Surface Finish

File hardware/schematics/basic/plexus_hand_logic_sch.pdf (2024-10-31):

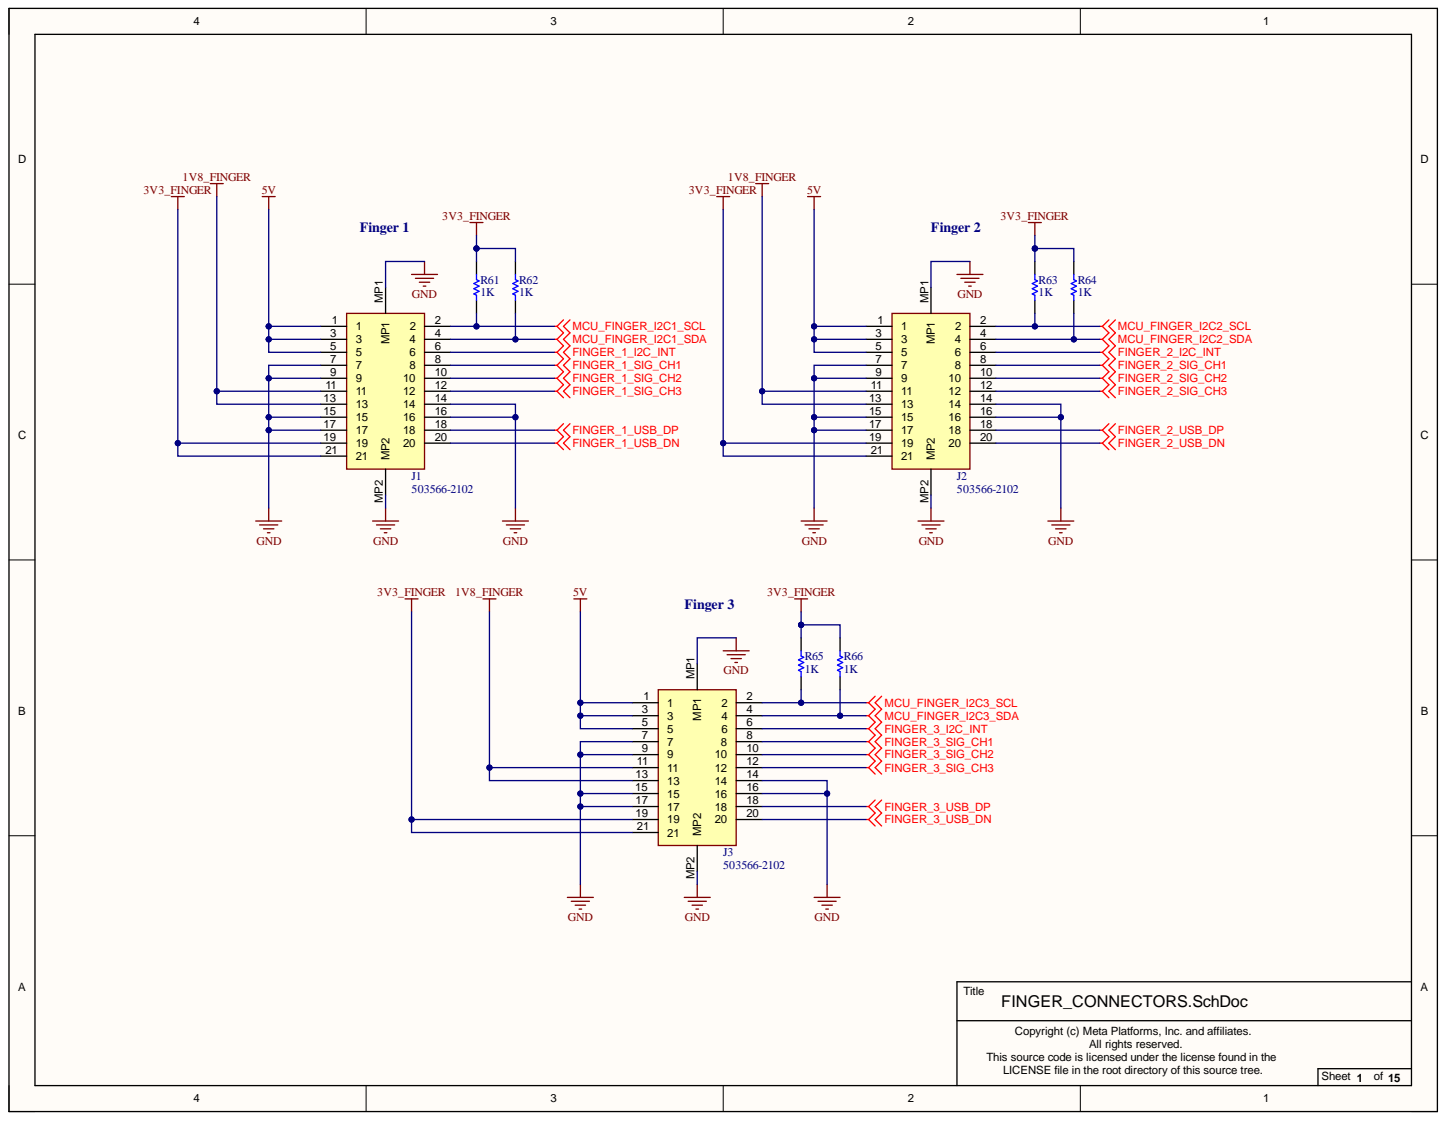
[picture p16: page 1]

Copyright (c) Meta Platforms, Inc. and affiliates.

This source code is licensed under the license found in the
LICENSE file in the root directory of this source tree.

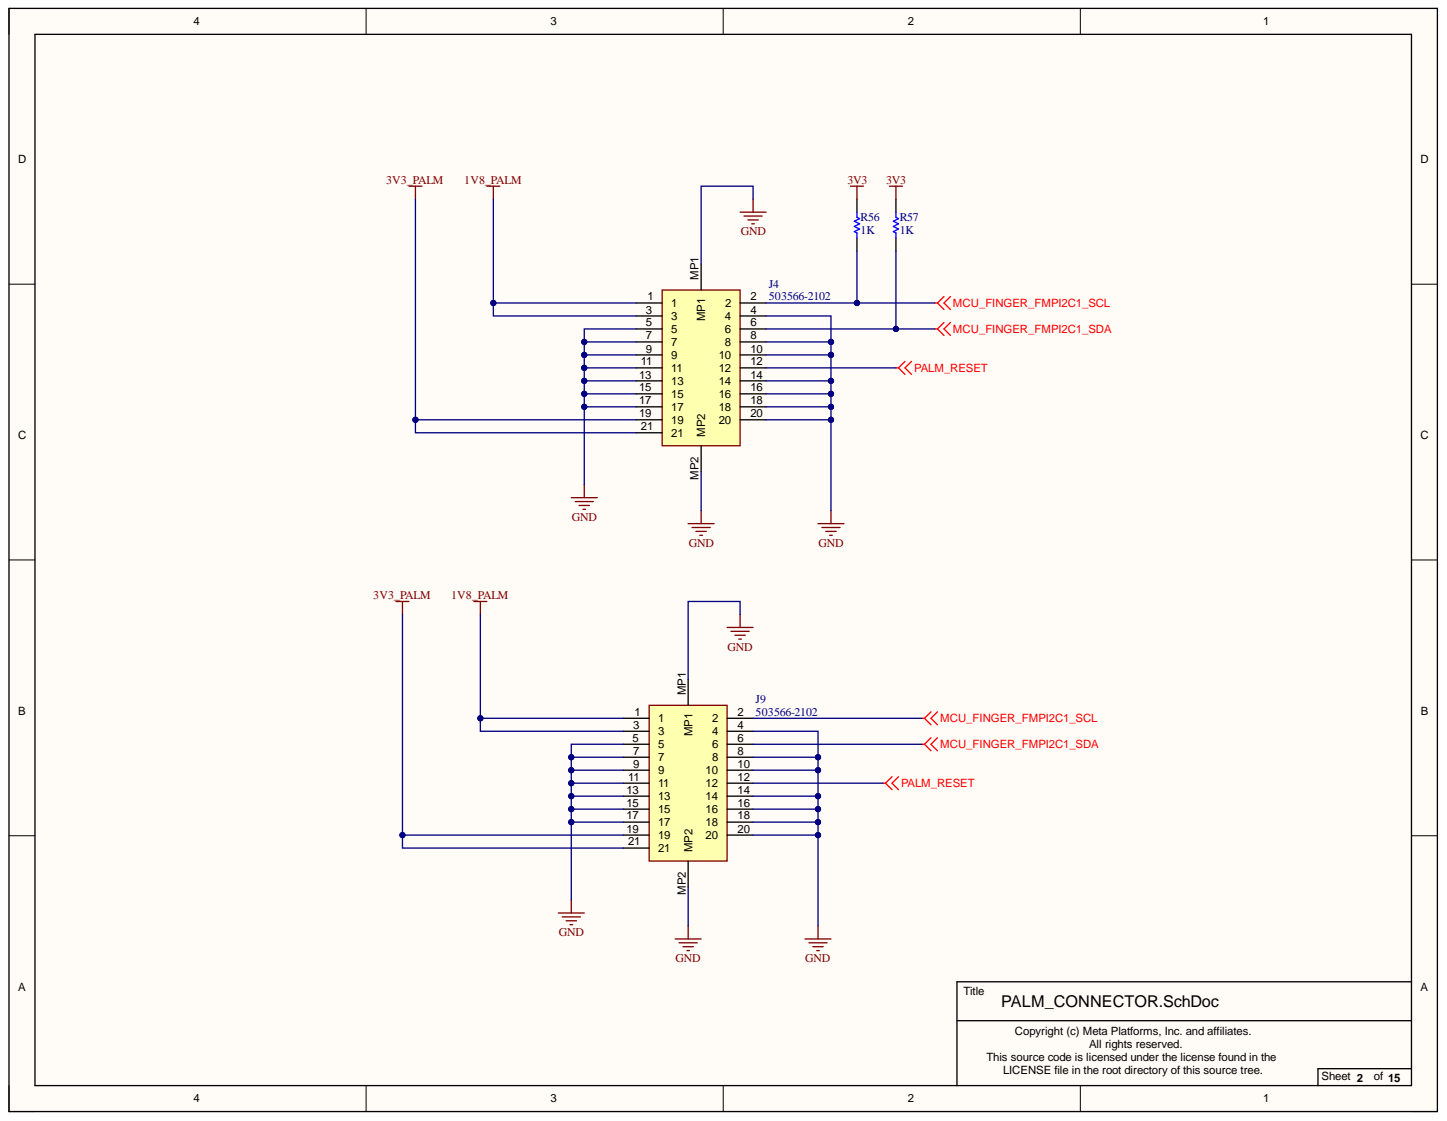
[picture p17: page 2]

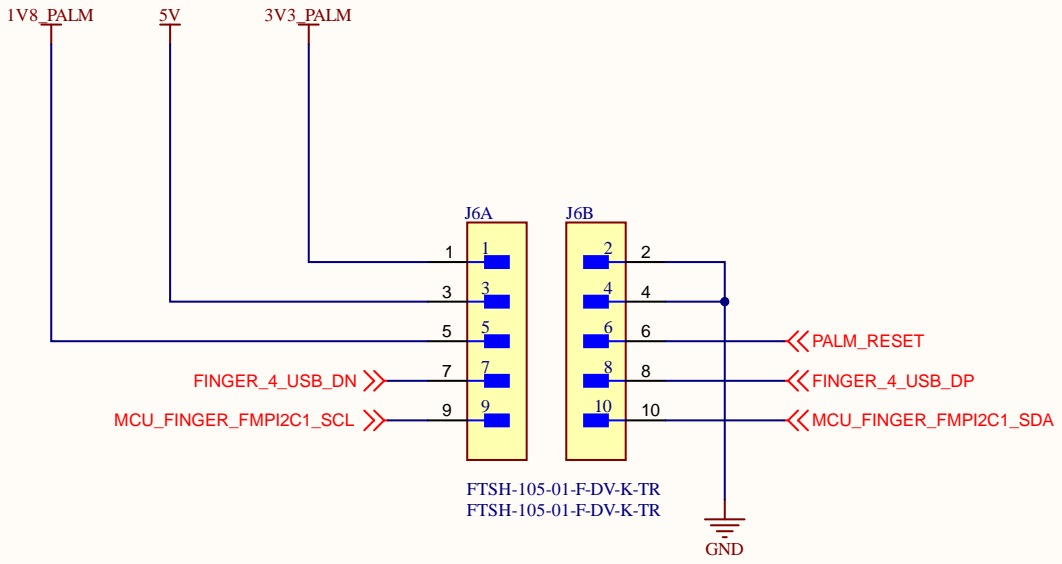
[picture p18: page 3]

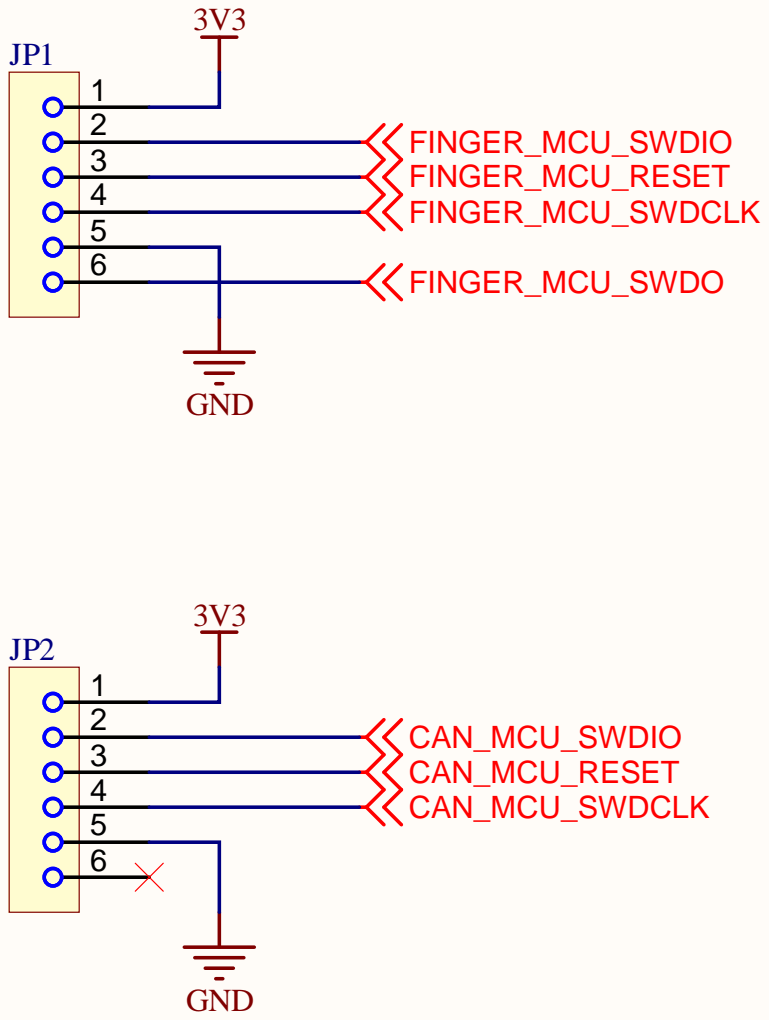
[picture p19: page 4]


IN+ 1
IN+ 2



VDD 48
VDDA 9
VDDIO2 36

CAN_USB_D1_N CAN_USB_D1_P 3V3 R71 10K | | VBAT 1


XOUT

VDD 32

VDD 64





Switching regulators
are set to forced
PWM mode



R 5 8
1 5 0 K | 7


1 8 | 3 2 1 1

2 3 | 5 4 1 9
2 4

2 0
1 6

1 3
1 7

1 6 | D G


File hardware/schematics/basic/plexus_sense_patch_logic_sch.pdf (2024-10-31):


Copyright (c) Meta Platforms, Inc. and affiliates.

This source code is licensed under the license found in the
LICENSE file in the root directory of this source tree.





Address selection:
Populate the following 0 ohm resistors:

If required, populate with 100K

SCL 12 SDA 13 A0 1

A1 2
INT 11


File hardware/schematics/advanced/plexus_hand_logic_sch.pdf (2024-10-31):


Copyright (c) Meta Platforms, Inc. and affiliates.

This source code is licensed under the license found in the
LICENSE file in the root directory of this source tree.




IN+ 1
IN+ 2


R 5 8
1 5 0 K | 7


VDD 48
VDDA 9
VDDIO2 36



Copyright (c) Meta Platforms, Inc. and affiliates.

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



F2_USB_D_N F2_USB_D_P

F3_USB_D_N F3_USB_D_P

CAN_USB_D1_N CAN_USB_D1_P FINGER_MCU_USB_DP_N FINGER_MCU_USB_DP_P

SUSP IND/LOCAL PWR/NON REM0 45

VDD33CR 24
VDD33PLL 64

Copyright (c) Meta Platforms, Inc. and affiliates.

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


2 3
1 0
2 9
3 6
1 4


VDD33 23
VDDA33 10
VDDA33 29
VDDA33 36

VBUS DET 27

R75 10K F2_USB_SDA | SDA/SMBDATA/NON REM1 22

R77 10K | HS IND/CFGSEL1 25

XTAL2 32

RBIAS 35


VDD33 23
VDDA33 10
VDDA33 29
VDDA33 36
VDDCR12 14

VBUS DET 27

R86 10K F3_USB_SDA | SDA/SMBDATA/NON REM1 22

R88 10K | HS IND/CFGSEL1 25

GND | 2

VSS 2


VDDA33 10
VDDA33 29
VDDA33 36
VDDCR12 14

VBUS DET 27

R97 10K F4_USB_SDA | SDA/SMBDATA/NON REM1 22

R99 10K | HS IND/CFGSEL1 25



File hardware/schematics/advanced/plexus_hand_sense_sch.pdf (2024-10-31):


Copyright (c) Meta Platforms, Inc. and affiliates.

This source code is licensed under the license found in the
LICENSE file in the root directory of this source tree.




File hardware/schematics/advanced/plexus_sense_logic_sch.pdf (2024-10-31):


Copyright (c) Meta Platforms, Inc. and affiliates.

This source code is licensed under the license found in the
LICENSE file in the root directory of this source tree.





2 2
2 1
2 0



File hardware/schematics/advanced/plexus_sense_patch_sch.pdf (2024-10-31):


Copyright (c) Meta Platforms, Inc. and affiliates.

This source code is licensed under the license found in the
LICENSE file in the root directory of this source tree.


Copyright (c)MetaPlatforms, Inc. and affiliates.

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


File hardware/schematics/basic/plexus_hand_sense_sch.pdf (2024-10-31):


Copyright (c) Meta Platforms, Inc. and affiliates.

This source code is licensed under the license found in the
LICENSE file in the root directory of this source tree.




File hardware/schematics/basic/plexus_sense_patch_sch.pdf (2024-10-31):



Copyright (c) Meta Platforms, Inc. and affiliates.

This source code is licensed under the license found in the
LICENSE file in the root directory of this source tree.


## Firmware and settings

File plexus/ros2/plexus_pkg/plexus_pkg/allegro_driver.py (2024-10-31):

#!/usr/bin/env python
#
# Copyright (c) Meta Platforms, Inc. and affiliates.
#
# This source code is licensed under the MIT license found in the
# LICENSE file in the root directory of this source tree.

# Install
# python -m pip install python-can

# Protocol
# http://wiki.wonikrobotics.com/AllegroHandWiki/images/e/eb/V4_AllegroHandUsersManual_1.1.pdf

import argparse
import math
import struct
import time
from enum import Enum
from typing import Any, List

import can
import numpy as np
from numpy.typing import NDArray

"""
http://wiki.wonikrobotics.com/AllegroHandWiki/index.php/CAN_Protocol_v4.0

0x20 (position requests)
 (000.000976)  can0  080   [0]  remote request
 (000.000079)  can0  084   [0]  remote request
 (000.000040)  can0  088   [0]  remote request
 (000.000059)  can0  08C   [0]  remote request
 (000.000044)  can0  080   [8]  CA FD BD FE 90 FF CE FF
 (000.000150)  can0  084   [8]  F9 FF CF FE 9A FF BE FF
 (000.000116)  can0  088   [8]  18 00 D3 FE A7 FF D6 FF
 (000.000174)  can0  08C   [8]  34 0A EF FF AF 00 FC FF
0x80 (info)
 (000.000143)  can0  200   [0]  remote request
 (000.000173)  can0  200   [7]  02 04 06 04 00 3C 05
0x38 (temp)
 (000.000241)  can0  0E0   [0]  remote request
 (000.000040)  can0  0E4   [0]  remote request
 (000.000039)  can0  0E8   [0]  remote request
 (000.000040)  can0  0EC   [0]  remote request
 (000.000040)  can0  0E0   [4]  2B 2A 29 25
 (000.000040)  can0  0E4   [4]  29 2B 29 27
 (000.000138)  can0  0E8   [4]  27 27 27 24
 (000.000081)  can0  0EC   [4]  30 26 24 F6
0x60 (set torque)
 (000.000209)  can0  180   [8]  02 00 CB 00 42 00 25 00
 (000.000079)  can0  184   [8]  01 00 B9 00 4A 00 33 00
 (000.000040)  can0  188   [8]  F1 FF C9 00 38 00 1F 00
 (000.000040)  can0  18C   [8]  58 02 05 00 8D FF FA FF
"""


class AllegroCommand(Enum):
    """
    https://github.com/simlabrobotics/allegro_hand_ros_v4/blob/master/src/allegro_hand_driver/src/candrv/candef.h
    """

    # Define CAN Command
    ID_CMD_SYSTEM_ON = 0x40
    ID_CMD_SYSTEM_OFF = 0x41
    ID_CMD_SET_TORQUE = 0x60
    ID_CMD_SET_TORQUE_1 = ID_CMD_SET_TORQUE + 0
    ID_CMD_SET_TORQUE_2 = ID_CMD_SET_TORQUE + 1
    ID_CMD_SET_TORQUE_3 = ID_CMD_SET_TORQUE + 2
    ID_CMD_SET_TORQUE_4 = ID_CMD_SET_TORQUE + 3
    ID_CMD_SET_POSE_1 = 0xE0
    ID_CMD_SET_POSE_2 = 0xE1
    ID_CMD_SET_POSE_3 = 0xE2
    ID_CMD_SET_POSE_4 = 0xE3
    ID_CMD_SET_PERIOD = 0x81
    ID_CMD_CONFIG = 0x68

    # Define CAN Data Reqeust (RTR)
    ID_RTR_HAND_INFO = 0x80
    ID_RTR_SERIAL = 0x88
    ID_RTR_FINGER_POSE = 0x20
    ID_RTR_FINGER_POSE_1 = ID_RTR_FINGER_POSE + 0
    ID_RTR_FINGER_POSE_2 = ID_RTR_FINGER_POSE + 1
    ID_RTR_FINGER_POSE_3 = ID_RTR_FINGER_POSE + 2
    ID_RTR_FINGER_POSE_4 = ID_RTR_FINGER_POSE + 3
    ID_RTR_IMU_DATA = 0x30
    ID_RTR_TEMPERATURE = 0x38
    ID_RTR_TEMPERATURE_1 = ID_RTR_TEMPERATURE + 0
    ID_RTR_TEMPERATURE_2 = ID_RTR_TEMPERATURE + 1
    ID_RTR_TEMPERATURE_3 = ID_RTR_TEMPERATURE + 2
    ID_RTR_TEMPERATURE_4 = ID_RTR_TEMPERATURE + 3

    @property
    def CAN_CMD_ID(self) -> int:
        return self.value << 2


class AllegroDriver:
    def __init__(self, can_channel: str = "can0", drain: bool = True) -> None:
        try:
            self.bus = can.Bus(
                interface="socketcan",
                channel=can_channel,
                can_filters=[
                    {
                        "can_id": AllegroCommand.ID_RTR_FINGER_POSE.CAN_CMD_ID,
                        "can_mask": 0xFF0,  # all finger pose 1111,1111,0000
                        "extended": False,
                    }  # get position
                ],
            )
        except OSError:
            self.bus = None
            raise RuntimeError(
                "CAN device not found, \
                    check if plexus USBC is plugged in, see trouble shooting here  \
                    https://python-can.readthedocs.io/en/stable/interfaces/socketcan.html"
            )

        self.misc_bus = can.Bus(
            interface="socketcan",
            channel=can_channel,
            can_filters=[
                {
                    "can_id": AllegroCommand.ID_RTR_HAND_INFO.CAN_CMD_ID,
                    "can_mask": 0xFFC,
                    "extended": False,
                },  # get info (0x80<<2)
                {
                    "can_id": AllegroCommand.ID_RTR_TEMPERATURE.CAN_CMD_ID,
                    "can_mask": 0xFF0,  # all finger temp 1111, 1111, 0000
                    "extended": False,
                },  # get temp (0x38<<2 - 0x3B <<2)
                {
                    "can_id": AllegroCommand.ID_RTR_SERIAL.CAN_CMD_ID,
                    "can_mask": 0xFFC,
                    "extended": False,
                },  # get serial(0x88 <<2)
            ],
        )

        # properly shutdown hand that's still running
        self.set_period()
        while drain:
            msg = self.bus.recv(timeout=0.005)
            if msg is not None:
                if msg.is_error_frame:
                    raise RuntimeError("CAN receiving error frame, check allegro hand")
                elif not msg.is_rx:
                    raise RuntimeError(
                        "Another program sending can command, you might have another driver running"
                    )
                else:
                    print(f"draining packet {msg}")
            else:
                break

    def shutdown(self) -> None:
        try:
            if self.bus:
                self.set_torque([0.0] * 16)
                self.set_motor(False)
                self.set_period(0, 0, 0, 0)
        except Exception as e:
            print(str(e))
        finally:
            if self.bus:
                self.bus.shutdown()
                self.misc_bus.shutdown()

    def __del__(self) -> None:
        self.shutdown()

    def send_msg(
        self,
        msg_id: int,
        data: Any = None,
        bus: can.Bus = None,
        is_remote_frame: bool = False,
    ) -> None:
        msg = can.Message(
            arbitration_id=msg_id << 2,
            data=data,
            is_remote_frame=is_remote_frame,
            is_extended_id=False,
        )

        if bus is None:
            bus = self.bus

        try:
            bus.send(msg)
        except can.exceptions.CanOperationError as e:
            print(e)
            raise RuntimeError(
                "can bus present, but not ready - did you turn on allegrohand"
            )

    def send_rtr_request(
        self, bus: can.Bus, msg_id: int, timeout: float = 0.01
    ) -> can.Message:
        self.send_msg(msg_id, is_remote_frame=True, bus=bus)
        msg = bus.recv(timeout)
        if msg is None:
            raise TimeoutError()
        assert (
            msg_id == msg.arbitration_id >> 2
        ), f"received remote frame \
            allegro msg_id {hex(msg.arbitration_id>>2)}(can msg_id = {hex(msg.arbitration_id)}>>2) \
            not match requested allegro msg_id {hex(msg_id)}"
        return msg

    def get_serial(self) -> str:
        msg = self.send_rtr_request(self.misc_bus, AllegroCommand.ID_RTR_SERIAL.value)
        return msg.data.decode().rstrip("\x00")

    def get_temp(self) -> List[int]:
        temp: List[int] = []
        for finger in range(4):
            msg_id = AllegroCommand.ID_RTR_TEMPERATURE.value + finger
            msg = self.send_rtr_request(self.misc_bus, msg_id=msg_id)
            assert msg.arbitration_id >> 2 == msg_id, "received wrong packet"
            try:
                temp += struct.unpack("4B", msg.data)
            except struct.error as e:
                print(msg)
                raise e
        return temp

    def get_joint_pos(self) -> NDArray:
        temp: List[float] = []
        for finger in range(4):
            msg = self.send_rtr_request(
                self.bus, msg_id=AllegroCommand.ID_RTR_FINGER_POSE.value + finger
            )
            temp += struct.unpack("4h", msg.data)
        return np.array(temp) * math.pi / 180 * 333 / 65536

    def get_info(self) -> dict:
        msg = self.send_rtr_request(
            self.misc_bus, msg_id=AllegroCommand.ID_RTR_HAND_INFO.value
        )
        hw_ver, fw_ver, is_left_hand, palm_temp, stat = struct.unpack("hhbBB", msg.data)
        return {
            "hw_ver": hex(hw_ver),
            "sw_ver": hex(fw_ver),
            "hand": "left" if is_left_hand else "right",
            "palm_temp": palm_temp,
            "stat": hex(stat),
            "motor": bool(stat & 0x1),
            "joint_temp_fault": bool(stat & 0x2),
            "joint_temp_throttle": bool(stat & 0x4),
            "joint_comm_fault": bool(stat & 0x8),
            "palm_temp_fault": bool(stat & 0x10),
        }

    def set_motor(self, is_on: bool) -> None:
        print(f"motor {is_on}")
        if is_on:
            self.send_msg(msg_id=AllegroCommand.ID_CMD_SYSTEM_ON.value)
        else:
            self.send_msg(msg_id=AllegroCommand.ID_CMD_SYSTEM_OFF.value)

    def set_torque(self, torqueN: List[float]) -> None:
        # https://github.com/0wu/ros-allegro/blob/ros2-main/ros-allegro/allegro_hand_driver/src/AllegroHandDrv.cpp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
        # PWM Range (-1200, 1200)
        assert len(torqueN) == 16
        torquePWM = list(map(lambda x: int(min(max(-1.0, x), 1.0) * 1200.0), torqueN))
        for finger in range(4):
            data = struct.pack("4h", *torquePWM[finger * 4 : finger * 4 + 4])
            self.send_msg(
                msg_id=AllegroCommand.ID_CMD_SET_TORQUE.value + finger, data=data
            )

    def set_period(
        self, joint_pos: int = 0, imu: int = 0, temp: int = 0, status: int = 0
    ) -> None:
        data = struct.pack("HHHH", joint_pos, imu, temp, status)
        self.send_msg(msg_id=AllegroCommand.ID_CMD_SET_PERIOD.value, data=data)


def test_torque(can_channel: str) -> None:
    print("==== Testing {} ====".format(can_channel))
    robot = AllegroDriver(can_channel=can_channel)
    t = time.perf_counter()
    for i in range(3):
        print(robot.get_temp())
        print(time.perf_counter() - t)
    print(robot.get_serial())

    robot.set_torque([0] * 16)
    robot.set_motor(True)
    for i in range(3):
        robot.set_torque(
            [
                -0.0,
            ]
            * 16
        )
        with np.printoptions(
            linewidth=100,
            formatter={"float": lambda x: np.format_float_positional(x, precision=2)},
        ):
            print("hand status", robot.get_info())
            print("joint position", robot.get_joint_pos())
        time.sleep(0.003)


def main() -> None:
    parser = argparse.ArgumentParser()
    parser.add_argument(
        "--can_channel", default=None, type=str, help="can channel, empty for all"
    )
    args = parser.parse_args()

    if args.can_channel is None:
        interfaces = can.detect_available_configs(interfaces="socketcan")
        for iface in interfaces:
            test_torque(iface["channel"])
    else:
        test_torque(args.can_channel)


if __name__ == "__main__":
    main()

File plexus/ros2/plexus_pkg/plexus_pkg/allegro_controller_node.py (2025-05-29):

#!/usr/bin/env python3

# Copyright (c) Meta Platforms, Inc. and affiliates.
# All rights reserved.

# This source code is licensed under the license found in the
# LICENSE file in the root directory of this source tree.



from typing import List
import numpy as np
import argparse

import rclpy
from rclpy.utilities import remove_ros_args
import rclpy.node
import rclpy.executors
from sensor_msgs.msg import JointState
from std_msgs.msg import String
from rclpy.qos import qos_profile_system_default
from rcl_interfaces.msg import SetParametersResult, Parameter

from plexus.ros2.plexus_pkg.plexus_pkg.allegro_driver import AllegroDriver

class ROSAllegroController(rclpy.node.Node):
    def __init__(self) -> None:
        super().__init__('allegro_controller')

        self.declare_parameter('can_interface', 'can0')
        try:
            self.robot = AllegroDriver(can_channel=self.get_parameter('can_interface').value)
        except RuntimeError as e:
            self.get_logger().fatal(str(e))
            raise e
        self.dt = 0.003
        self.dof = 16
        self.timeout = 30_000_000_000

        #controller gains
        for i in range(16):
            self.declare_parameter(f'gains_pd/{i}/p', 6.)
            self.declare_parameter(f'gains_pd/{i}/d', 0.15)
            self.declare_parameter(f'position_offset/{i}', 0.)
        self.declare_parameter(f'qv_alpha', 0.7)
        self.declare_parameter('torque_limit', 0.5)
        self.q_des = None

        # state
        self.joint_state_publisher = self.create_publisher(JointState, "joint_states", qos_profile_system_default)
        self.joint_target_sub = self.create_subscription(JointState, "joint_cmd", self.joint_cmd_cb, qos_profile_system_default)
        self.lib_cmd_sub = self.create_subscription(String, "lib_cmd", self.lib_cmd_cb, qos_profile_system_default)
        self.add_on_set_parameters_callback(self.param_cb)

        self.create_timer(self.dt, self.control_loop)

        self.q = None
        self.prev_q = None
        self.qv = None
        self.torque_des = None
        self.motor_status = None

        self.last_control = self.get_clock().now()

    def param_cb(self, param: List[Parameter]) -> SetParametersResult:
        for p in param:
            print(f'param update {p.name}: {p.value}')
        return SetParametersResult(successful=True)

    def lib_cmd_cb(self, msg: String) -> None:
        if msg.data == "home":
            q_home= np.zeros(16)
            q_home[12] = 0.4
            self._move_joint(q_home, torque_target=False)
        elif msg.data == "off":
            self._set_motor(False)

    def joint_cmd_cb(self, msg: JointState) -> None:
        if len(msg.position) > 0 and len(msg.effort) > 0:
            self.get_logger().error(f"received both position and effort commands, ignoring")
            return

        if len(msg.position) == 16:
            self._move_joint(msg.position, torque_target=False)
        elif len(msg.effort) == 16:
            self._move_joint(msg.effort, torque_target=True)
        else:
            self.get_logger().warning(f'invalid cmd: {msg}')

    def _set_motor(self, is_on: bool):
        if self.motor_status is None or self.motor_status != is_on:
            self.robot.set_motor(is_on)
            self.get_logger().info(f"motor switched {is_on}")
        self.motor_status = is_on 

    def _move_joint(self, target_cmd, torque_target=False):
        if torque_target:
            if self.q_des is not None: 
                self.get_logger().info(f"switching to torque mode")
            self.q_des = None
            self.torque_des = np.array(target_cmd)
        else:
            if self.torque_des is not None: 
                self.get_logger().info(f"switching to position mode")
            self.q_des = np.array(target_cmd)
            self.torque_des = None
        self.cmd_updatetime = self.get_clock().now()
        self._set_motor(True)

    def control_loop(self) -> None:

        # timing
        start_control = self.get_clock().now()
        interval = start_control - self.last_control
        self.last_control = start_control

        # getting parameters
        self.kp = np.array([self.get_parameter(f'gains_pd/{i}/p').value for i in range(self.dof)])
        self.kd = np.array([self.get_parameter(f'gains_pd/{i}/d').value for i in range(self.dof)])
        self.position_offset= np.array([self.get_parameter(f'position_offset/{i}').value for i in range(self.dof)])
        qv_alpha = self.get_parameter('qv_alpha').value

        if self.q is not None:
            self.prev_q = self.q 

        self.q = self.robot.get_joint_pos() + self.position_offset

        #initialize
        if self.prev_q is None:
            self.prev_q = self.q

        #velocity estimate
        qv_findiff = (self.q - self.prev_q) / (interval.nanoseconds /1e9)
        if self.qv is None:
            self.qv = qv_findiff
        else:
            self.qv = (1-qv_alpha) * self.qv + qv_alpha * qv_findiff

        if self.q_des is None and self.torque_des is None:
            self._move_joint(self.q, torque_target=False)        

        if self.torque_des is None:
            #PD
            err = self.q_des - self.q
            torque = self.kp * err - self.kd * self.qv
        else:
            torque = self.torque_des

        torque_limit = self.get_parameter('torque_limit').value
        torque = np.clip(torque, -torque_limit, torque_limit)
        self.robot.set_torque(torque)

        if (start_control - self.cmd_updatetime ).nanoseconds > self.timeout:
            self._set_motor(False)

        #publish
        msg = JointState()
        msg.header.stamp = self.get_clock().now().to_msg()
        msg.name = [f'allegro_joint_{i}.0' for i in range(16)]
        msg.position = self.q.tolist()
        msg.velocity = self.qv.tolist()
        msg.effort = torque.tolist()
        self.joint_state_publisher.publish(msg)

        # check timing 
        if interval.nanoseconds/1e9 > 2.0 * self.dt:
            self.get_logger().warning(f'slow control loop {interval.nanoseconds/1e9} > {self.dt}', throttle_duration_sec=1)

        control_time = self.get_clock().now() - start_control
        if control_time.nanoseconds/1e9 > self.dt * 0.9:
            self.get_logger().warn(f"control time {control_time.nanoseconds/1e9} near/over {self.dt}", throttle_duration_sec=1)


def main() -> None:
    rclpy.init()
    try:
        pdnode = ROSAllegroController()
        rclpy.spin(pdnode)
    except KeyboardInterrupt:
        pass
    except RuntimeError as e:
        print("ERROR")


if __name__ == '__main__':
    main()

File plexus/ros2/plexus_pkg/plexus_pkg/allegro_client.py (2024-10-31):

# Copyright (c) Meta Platforms, Inc. and affiliates.
#
# This source code is licensed under the MIT license found in the
# LICENSE file in the root directory of this source tree.
#
# --------------------------------------------------------
# Based on:
# https://github.com/felixduvallet/allegro-hand-ros/blob/master/allegro_hand/src/allegro_hand/liballegro.py
# --------------------------------------------------------

import traceback
from typing import List, Tuple, Union

from rcl_interfaces.msg import Parameter, ParameterType, ParameterValue
from rclpy.node import Node
from rclpy.parameter_service import GetParameters, SetParameters
from sensor_msgs.msg import JointState
from std_msgs.msg import String


class AllegroRobot(Node):
    def __init__(
        self, hand_topic_prefix: str = "allegroHand", num_joints: int = 16
    ) -> None:
        """Simple python interface to the Allegro Hand.

        The AllegroClient is a simple python interface to an allegro
        robot hand.  It enables you to command the hand directly through
        python library calls (joint positions, joint torques, or 'named'
        grasps).

        The constructors sets up publishers and subscribes to the joint states
        topic for the hand.

        Note on hand topic names: The default topic (allegroHand/foo) can be
        remapped to a different topic prefix (allegroHand_0/foo) in one of two
        ways:
          1. pass in allegroHand_0 as the hand_topic_prefix
          2. remap *each* topic on the command line
             (allegroHand/joint_cmd:=allegroHand_0/joint_cmd)
        The first method is probably easier.

        :param hand_topic_prefix: The prefix to use for *all* hand
        topics (publishing & subscribing).

        :param num_joints: Number of expected joints, used when
        commanding joint positions.

        """
        super().__init__("hand_commander")

        # Topics (that can be remapped) for named graps
        # (ready/envelop/grasp/etc.), joint commands (position and
        # velocity), joint state (subscribing), and envelop torque. Note that
        # we can change the hand topic prefix (for example, to allegroHand_0)
        # instead of remapping it at the command line.
        hand_topic_prefix = hand_topic_prefix.rstrip("/")
        topic_grasp_command = "{}/lib_cmd".format(hand_topic_prefix)
        topic_joint_command = "{}/joint_cmd".format(hand_topic_prefix)
        topic_joint_state = "{}/joint_states".format(hand_topic_prefix)

        # Publishers for above topics.
        self.pub_grasp = self.create_publisher(String, topic_grasp_command, 10)
        self.pub_joint = self.create_publisher(JointState, topic_joint_command, 10)
        self.create_subscription(
            JointState, topic_joint_state, self._joint_state_callback, 10
        )
        self._joint_state = None

        self._num_joints = num_joints

        self.get_logger().info(
            "Allegro Client start with hand topic: {}".format(hand_topic_prefix)
        )

        # "Named" grasps are those provided by the bhand library. These can be
        # commanded directly and the hand will execute them. The keys are more
        # human-friendly names, the values are the expected names from the
        # allegro controller side. Multiple strings mapping to the same value
        # are allowed.
        self._named_grasps_mappings = {
            "home": "home",
            "off": "off",
            # "gravity_compensation": "gravcomp",
            # "gravity compensation": "gravcomp",
            # "gravity": "gravcomp",
            # "ready": "ready",
            # "three_finger_grasp": "grasp_3",
            # "three finger grasp": "grasp_3",
            # "four_finger_grasp": "grasp_4",
            # "four finger grasp": "grasp_4",
            # "index_pinch": "pinch_it",
            # "index pinch": "pinch_it",
            # "middle_pinch": "pinch_mt",
            # "middle pinch": "pinch_mt",
            # "envelop": "envelop",
        }
        self.joint_names = [f"allegro_joint_{i}.0" for i in range(self._num_joints)]

    def disconnect(self) -> None:
        """
        Disconnect the allegro client from the hand by sending the 'off'
        command. This is principally a convenience binding.

        Note that we don't actually 'disconnect', so you could technically
        continue sending other commands after this.
        """
        self.command_hand_configuration("off")

    def _joint_state_callback(self, data: JointState) -> None:
        self._joint_state = data

    def get_p_gain(self) -> List[float]:
        client = self.create_client(
            GetParameters, "/allegroHand/allegro_controller/get_parameters"
        )
        ready = client.wait_for_service(timeout_sec=5.0)
        if not ready:
            raise RuntimeError("Wait for service timed out")

        request = GetParameters.Request()
        request.names = [f"gains_pd/{i}/p" for i in range(self.num_joints)]
        result = client.call(request)
        return [v.double_value for v in result.values]

    def set_p_gain(self, gain: List[float]) -> None:
        client = self.create_client(
            SetParameters, "/allegroHand/allegro_controller/set_parameters"
        )
        ready = client.wait_for_service(timeout_sec=5.0)
        if not ready:
            raise RuntimeError("Wait for service timed out")

        request = SetParameters.Request()
        request.parameters = [
            Parameter(
                name=f"gains_pd/{i}/p",
                value=ParameterValue(
                    type=ParameterType.PARAMETER_DOUBLE, double_value=gain[i]
                ),
            )
            for i in range(self.num_joints)
        ]
        result = client.call(request)
        assert all(
            [result.results[i].successful for i in range(self.num_joints)]
        ), "gain setting failed"

    def command_joint_position(self, desired_pose: List) -> bool:
        """
        Command a specific desired hand pose.

        The desired pose must be the correct dimensionality (self._num_joints).
        Only the pose is commanded, and **no bound-checking happens here**:
        any commanded pose must be valid or Bad Things May Happen. (Generally,
        values between 0.0 and 1.5 are fine, but use this at your own risk.)

        :param desired_pose: The desired joint configurations.
        :return: True if pose is published, False otherwise.
        """

        # Check that the desired pose can have len() applied to it, and that
        # the number of dimensions is the same as the number of hand joints.
        if (
            not hasattr(desired_pose, "__len__")
            or len(desired_pose) != self._num_joints
        ):
            self.get_logger().warn(
                "Desired pose must be a {}-d array: got {}.".format(
                    self._num_joints, desired_pose
                )
            )
            return False
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

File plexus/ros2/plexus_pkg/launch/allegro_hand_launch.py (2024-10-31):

# Copyright (c) Meta Platforms, Inc. and affiliates.
# All rights reserved.

# This source code is licensed under the license found in the
# LICENSE file in the root directory of this source tree.

#!/usr/bin/env python3
import os
from pathlib import Path
from launch import LaunchDescription
from launch.actions import (
    RegisterEventHandler,
    EmitEvent,
    LogInfo,
    OpaqueFunction,
)
from launch.event_handlers import OnProcessExit
from launch.events import Shutdown
from launch_ros.actions import Node
from plexus.ros2.plexus_pkg.plexus_pkg.allegro_driver import AllegroDriver
import can
from typing import Dict

def get_allegro_configs() -> Dict[str, Path]:
    launch_root = os.path.dirname(os.path.abspath(__file__))
    interfaces=can.detect_available_configs(interfaces="socketcan")
    configs = {}
    for iface in interfaces:
        allegro_driver = AllegroDriver(can_channel=iface["channel"])
        allegro_serial = allegro_driver.get_serial().lower()
        allegro_config_serial = Path(f"{launch_root}/allegro_node_params_{allegro_serial}.yaml")
        allegro_config_default= Path(f"{launch_root}/allegro_node_params.yaml")
    
        if allegro_config_serial.exists():
            print(f'using hand specific config - {allegro_config_serial.absolute()}')
            configs[iface["channel"]] = allegro_config_serial
        else:
            print(f'using default config - {allegro_config_default.absolute()}')
            configs[iface["channel"]] = allegro_config_default

    return configs


def _generate_launch_description(context):
    configs = get_allegro_configs()
    nodes = []
    for i, (can_interface, config) in enumerate(configs.items()):
        _ns = f"allegroHand{i}" if i > 0 else "allegroHand"
        allegro_controller_node  = Node(
            namespace=_ns,
            package="plexus_pkg",
            executable="allegro_controller_node.py",
            name="allegro_controller",
            parameters=[config, {"can_interface": can_interface}],
            respawn=True
        )
        nodes.append(allegro_controller_node)

        allegro_info_node  = Node(
            namespace=_ns,
            package="plexus_pkg",
            executable="allegro_info_node.py",
            name="allegro_info",
            parameters=[config, {"can_interface": can_interface}],
        )
        nodes.append(allegro_info_node)


        shutdown_action = RegisterEventHandler(
            OnProcessExit(
                target_action=allegro_controller_node,
                on_exit=[
                    LogInfo(msg="critical node failure"),
                    EmitEvent(event=Shutdown(
                        reason='critical node failure'))
                ]
            )
        )
        nodes.append(shutdown_action)
    return nodes

def generate_launch_description():
    return LaunchDescription([OpaqueFunction(function=_generate_launch_description)])
